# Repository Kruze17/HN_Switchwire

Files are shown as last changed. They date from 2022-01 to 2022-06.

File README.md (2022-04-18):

# HN Switchwire
## Serial Request Video (Playable):
Serial Request (https://www.youtube.com/watch?v=LyNLB14Rkbk)
## This repository hosts the files that are needed to the build my version of the Voron Switchwire from Ender 3 Pro.  

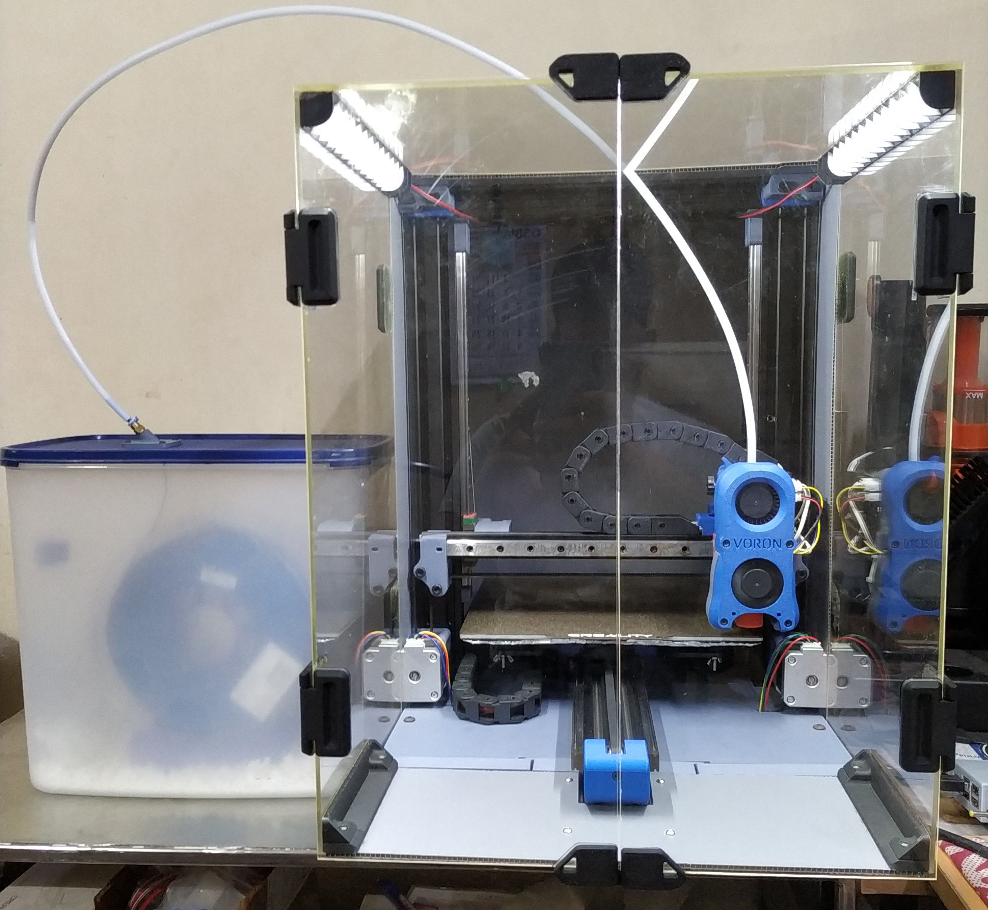
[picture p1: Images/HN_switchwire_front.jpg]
  
### ***These are the repositories you will need to visit in order to get required STL files and more information. I just simply cannot host them in my repo as the creators have put so much effort and time in building and documenting their own versions of designs. Peace.***  
  
[DaRk_dOg's](https://github.com/boubounokefalos) Ender_SW: https://github.com/boubounokefalos/Ender_SW  
[Badnoob's](https://github.com/VoronDesign/VoronUsers/tree/master/printer_mods/Badnoob) AB BN 30: https://github.com/VoronDesign/VoronUsers/tree/master/printer_mods/Badnoob/AB-BN  
~~[M. Kanawati's](https://github.com/kanawati975) BL Touch X-carriage mod for Switchwire: https://github.com/kanawati975/Voron_Switchwire/tree/main/BL-Touch~~  
[henrikssn's](https://github.com/henrikssn) Euler Extruder: https://github.com/henrikssn/VoronUsers/tree/euler/printer_mods/henrikssn/euler_extruder  
[Tripnutz's](https://www.thingiverse.com/tripnutz/designs) ePIc snapPI hinged pi case: https://www.thingiverse.com/thing:2747502
###### Update 09-02-2022
```
1. The X-carriage BL Touch mod for Switchwire was made for e3d V6 Hotend only. So i have decided to drop it.
   After several suggestions regarding the BL touch not perforimg well in a fully enclosed printer, i decided to
   go with an inductive probe. But it's creator M. Kanawati was kind enough to offer me custom design files
   sepcific for my hotend. But as i have said, i am moving towards inductive probe.

2. Added the rail guides for MGN12H linear rails and 4040 extrusion rail guide as per subscribers' request.

3. Added the modified the x-axis drag chain anchor for euler extruder for switchwire, in case you guys want it.
```
###### Update 28-02-2022
```
1. Added my printer's hartk Toolhead PCB rev3.2 wiring diagram with Creality v4.2.2 board.

2. Added my printer's klipper config files for user reference.
```
###### Update 7-03-2022
```
1. Added my printer's slicer configs.
```
###### Update 29-03-2022
```
1. Added the stl file for modified 6mm filament feed slot
2. Added the stl files for my custom pi case
```

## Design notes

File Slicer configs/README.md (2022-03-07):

## Changes that you might want to do to my slicer configs:
### Set your bed dimensions:
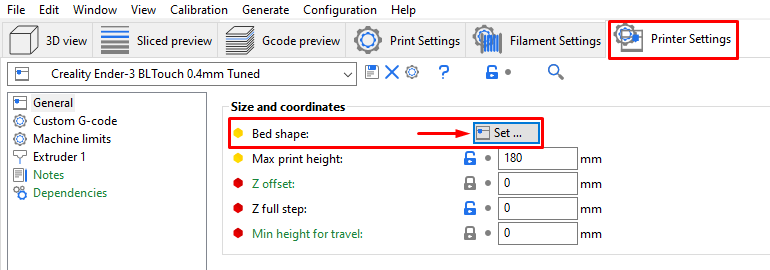
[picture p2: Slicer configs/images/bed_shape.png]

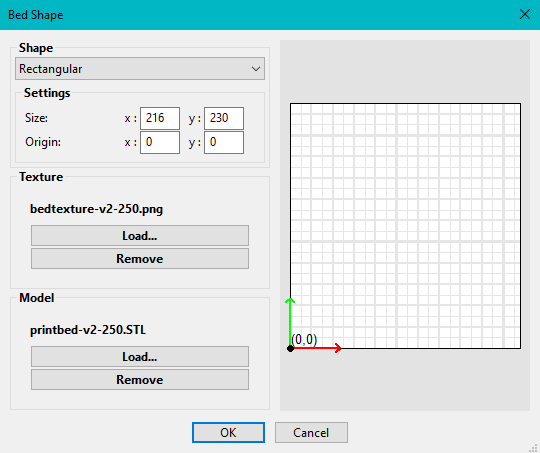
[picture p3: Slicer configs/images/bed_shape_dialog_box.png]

### Load a custom bed texture and model:
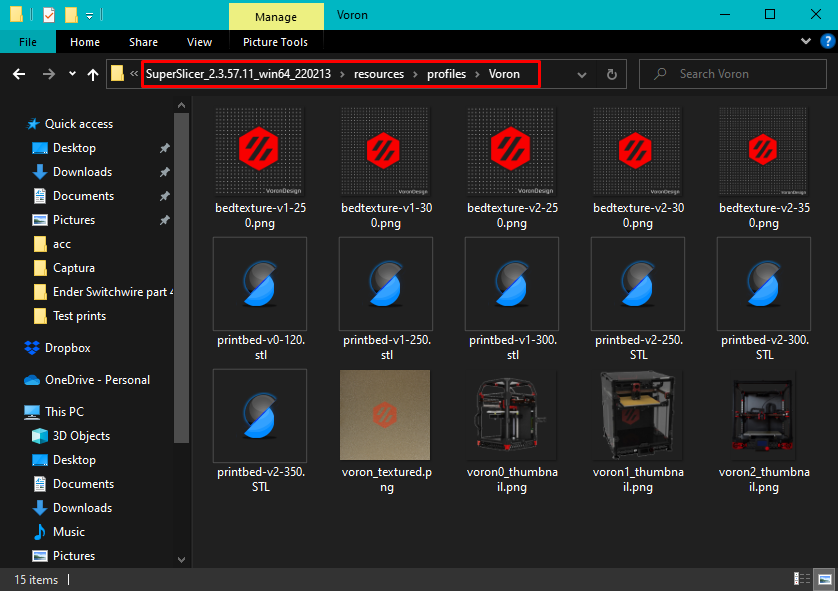
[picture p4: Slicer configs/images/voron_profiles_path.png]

### Change the custom gcode settings:
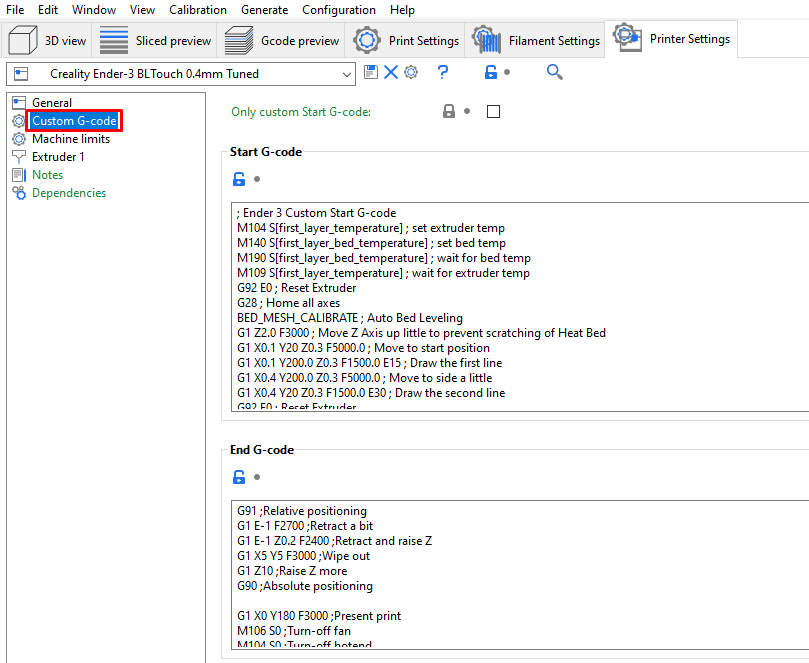
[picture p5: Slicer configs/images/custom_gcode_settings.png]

### Change retraction settings:
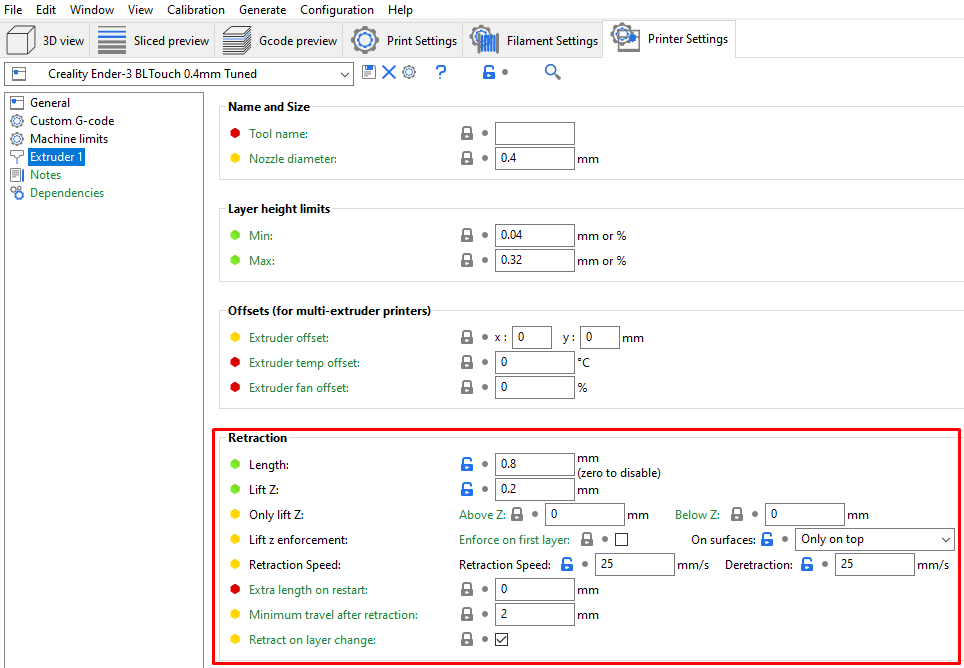
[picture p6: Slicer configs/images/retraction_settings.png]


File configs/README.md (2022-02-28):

## !!! Warning !!!
***Do no copy-paste or blindly use the configs! Use them with proper research and knowledge. I "do not" take any responsibility, if your printer gets damaged by using my configs.***   

I am using GCode shell command extension by [Arksine](https://github.com/Arksine) for my custom macros in client_macros.cfg file: https://github.com/th33xitus/kiauh/blob/master/docs/gcode_shell_command.md

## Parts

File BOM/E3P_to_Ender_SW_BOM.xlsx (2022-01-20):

Category | Component | Standard | Qty | Required for the Ender SW?
Filament | Primary Color (Black) |  | 1 | Yes
Filament | Secondary Color (Red) |  | 1 | Yes
Printed Parts | Printed Parts |  | 1 | Yes - STLs on GitHub (https://github.com/boubounokefalos/Ender_SW)
Fasteners | M2x10 Self Tapping Screw for Plastics |  | 6 | Updated according to Ender_SW BOM
Fasteners | M3x12 SHCS |  | 13
Fasteners | M3x14 BHCS |  | 2
Fasteners | M3x16 SHCS |  | 6
Fasteners | M3x20 SHCS |  | 8
Fasteners | M3x25 SHCS |  | 4
Fasteners | M3x30 SHCS |  | 26
Fasteners | M3x40 SHCS |  | 7
Fasteners | M3x6 FHCS |  | 12
Fasteners | M3x8 SHCS |  | 71
Fasteners | M4x20 SHCS |  | 2
Fasteners | M4x6 BHCS |  | 2
Fasteners | M5x10 BHCS |  | 10
Fasteners | M5x10 SHCS |  | 4
Fasteners | M5x16 BHCS |  | 5
Fasteners | M5x20 BHCS |  | 1
Fasteners | M5x20 SHCS |  | 8
Fasteners | M5x35 BHCS |  | 4
Fasteners | M5x40 SHCS |  | 8
Fasteners | M5x60 SHCS |  | 8
Fasteners | 6x6x3 Aluminium Spacer from Ender 3 |  | 4
Fasteners | M3 Heatset Insert |  | 54
Fasteners | M5 1mm Shim |  | 20
Fasteners | M3 Hexnut |  | 10
Fasteners | M3 T-nut (For 2020 extrusions) |  | 35 | Updated according to Ender_SW BOM
Fasteners | M5 T-nut (For 2020 extrusions) |  | 50 | Updated according to Ender_SW BOM
Motion | GT2 Open Belt LL-2GT-6 (6mm wide) - 1500mm |  | 2 | Yes
Motion | GT2 Open Belt LL-2GT-6 (6mm wide) - 800mm |  | 1 | Yes
Motion | GT2 20T (6mm wide) Pulley (5mm bore) |  | 3 | Yes
Motion | F695 2RS Bearing |  | 20 | Yes
Motion | Linear Rail MGN12H (300mm) |  | 5 | X -> 1, Y -> 2 and Z -> 2
Motion | Key-bak Super48 13oz |  | 1 | Yes
Vibration Management | Rubber Compressor Foot |  | 4 | Yes or you can use these printed feet (https://www.thingiverse.com/thing:4721832)
Electronics | Omron Mouse Button - Micro Switch |  | 2 | 1 - the Y axis microswitch is reused
Electronics | Omron TL-Q5MC2 - NPN, NC, 5mm Sense |  | 1 | Yes
Electronics | BAT85 Diode |  | 1 | Yes
Electronics | NEMA17 Motor 17HS15-1504S1 |  | 3 | New or Reused. If you have a gear puller, you can reuse these. I bought new ones. You also need the smaller motor for the afterburner.
Electronics | Mean Well LRS-350-24 PSU |  | 1 | Reused
Electronics | Mean Well RS-25-5 PSU |  | 1 | Yes
Electronics | ZF - Rocker Switches DPST 16A ON-OFF |  | 1 | No
Electronics | Fuse Medium Time Delay Acting 8A 250V Holder Cartridge 5 X 20mm Glass |  | 2 | Yes
Electronics | TycoElectronics - 10EGG1-2 (Normal) or 10EHG1-2 (Medical): Filtered Power Inlet |  | 1 | No
Electronics | IEC320 C14 Inlet - Push-fit - w/ Rocker Switch & Fuse |  | 1 | Yes
Electronics | 40x40x10 Axial Fan- Ball Bearing (24V) |  | 1 | Yes
Electronics | 40x40x20 Centrifugal Blower Fan - Ball Bearing (24V) |  | 1 | Depends on version of Afterburner
Electronics | 60x60x20 Axial Fan (24V) |  | 1 | Yes
Controller | RaspberryPi4 |  | 1 | Reused ( I was running Octoprint)
Controller | MicroSD Card |  | 1 | Reused
Controller | USB C Power Cable |  | 1 | Reused
Controller | SKR Mini E3 V2 |  | 1 | Reused or new. I had upgraded before the mod
Controller | USB Cable A-male Mini B-male (Included with SKR Mini) |  | 1 | A right angle USB mini is required
Controller | Mini 12864 Display (Type B) |  | 1 | Optional. I don't use one
Frame | Misumi 3060 x 520mm - HFSB6-3060-520-AH105-BH415-AV180 |  | 2 | Use Ender 3 Pro frame
Frame | Misumi 3030 x 400mm - HFSB6-3030-400-TPW |  | 2 | Use Ender 3 Pro frame
Frame | Misumi 3030 x 360mm - HFSB6-3030-360-LCH-RCH |  | 1 | Use Ender 3 Pro frame
Frame | Misumi 3030 x 300mm - HFSB6-3030-300-TPW |  | 2 | Use Ender 3 Pro frame
Frame | Misumi 2020 x 340mm - HFSB5-2020-340-AH15-BH325 |  | 1 | Use Ender 3 Pro frame
Frame | Misumi 2020 x 340mm - HFSB5-2020-340 |  | 1 | Use Ender 3 Pro frame
Misc | Bowden Tube (4mm OD, 3mm ID) |  | 3m | Reused
Misc | 6mm x 3mm Round Neodymium Magnets |  | 8 | No
Cables | Fork Spade Terminal |  | 15 | I have a various assorment of connectors as Voron recommends. The quantities may be off and everyone has their own preferences for wiring Yes
Cables | Insulated Crimp Receptical |  | 10 | Yes
Cables | Nylon Cable Ties 4" |  | 100 | Yes
Cables | MicroFit3 Male Pin (43031-0007) |  | 40 | Yes
Cables | MicroFit3 Female Pin (43030-0007) |  | 40 | Yes
Cables | MicroFit Connector Receptacle 4 Position (43645-0400) |  | 4 | Yes
Cables | MicroFit Connector Receptacle 3 Position (43645-0300) |  | 1 | Yes
Cables | MicroFit Connector Receptacle 2 Position (43645-0200) |  | 6 | Yes
Cables | MicroFit Connector Plug 4 Position (43640-0401) |  | 4 | Yes
Cables | MicroFit Connector Plug 3 Position (43640-0301) |  | 1 | Yes
Cables | MicroFit Connector Plug 2 Position (43640-0201) |  | 6 | Yes
Cables | JST-XH Female Pin |  | 40 | Yes
Cables | JST-XH Connector Plug 4 Position |  | 4 | Yes
Cables | JST-XH Connector Plug 3 Position |  | 4 | Yes
Cables | JST-XH Connector Plug 2 Position |  | 4 | Yes
Cables | 24AWG Silicone Cable (100ft total) |  | 1 | Yes
Cables | 16AWG Silicone Cable (10ft total) |  | 1 | Yes
Cables | 20AWG Silicone Cable (10ft total) |  | 1 | Yes
Cables | 10x11 Cable Chain - Openable (1m) |  | 2 | Yes
Panels | Opaque Enclosure Panels |  | 6 | No (https://www.michaels.com/corrugated-board-by-creatology/M10567770.html)
Panels | Side/Front/Top Acrylic Panels |  | 5 | No (https://www.tapplastics.com/product/plastics/cut_to_size_plastic/acrylic_sheets_clear/508)
Buildplate | Prusa MK52 Heated Bed - 24V |  | 1 | Reused Ender 3 bed
Buildplate | Spring Steel Sheet for Prusa MK52 Bed (included with TL Heated Bed) |  | 1
Buildplate | Prusa MK3 Y Carrier |  | 1
Afterburner |  |  |  | The Afterburner is unchanged. Check the BOM and sourcing guide

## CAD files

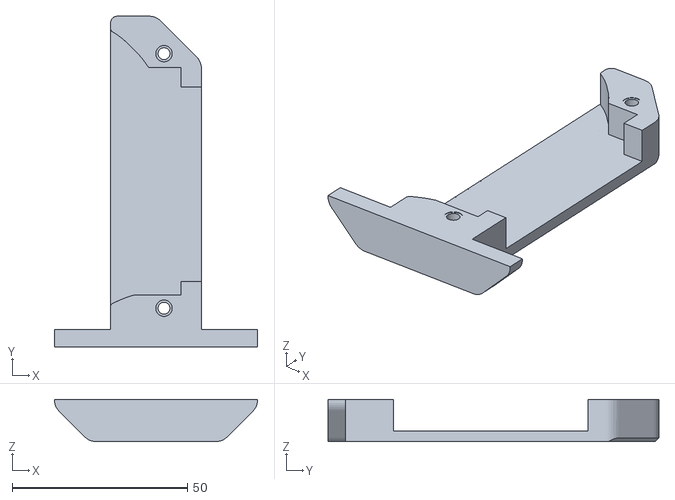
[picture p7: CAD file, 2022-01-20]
Keybak/SW_Alternative_keybak_a.stl
58.0 x 94.5 x 12.0

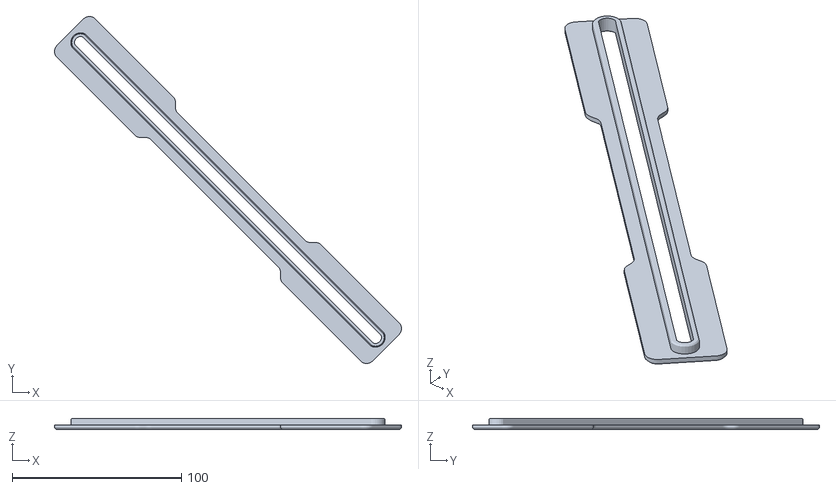
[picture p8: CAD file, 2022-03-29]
Modified feed slot/6mm_feed_slot.stl
205.3 x 205.3 x 6.40

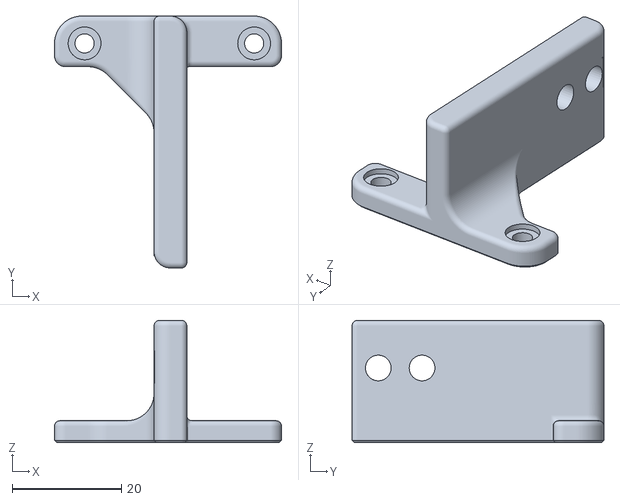
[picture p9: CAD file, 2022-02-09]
Modified X-chain Anchor(igus)/x_chain_anchor_igus_remixed.stl
41.5 x 46.1 x 22.3

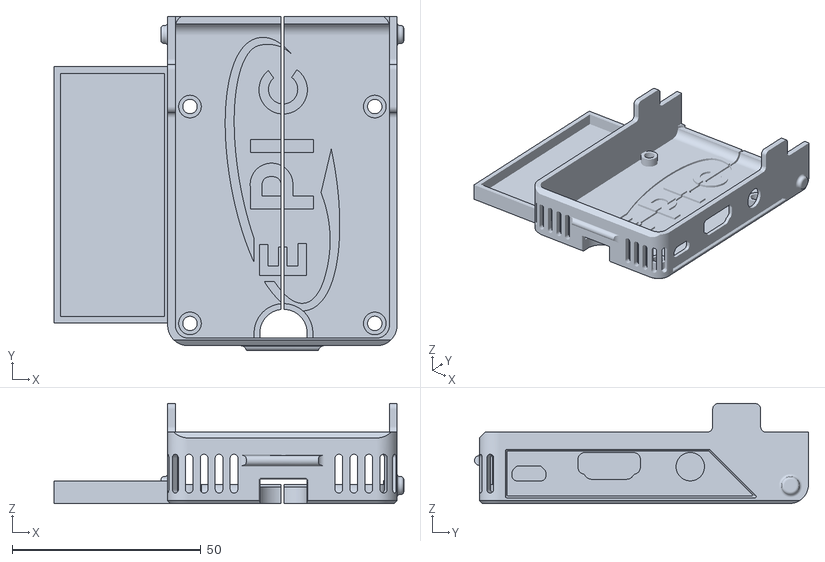
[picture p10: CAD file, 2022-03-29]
Pi 3b+ case/rpi3b+_base_v1.stl
92.7 x 88.6 x 26.5

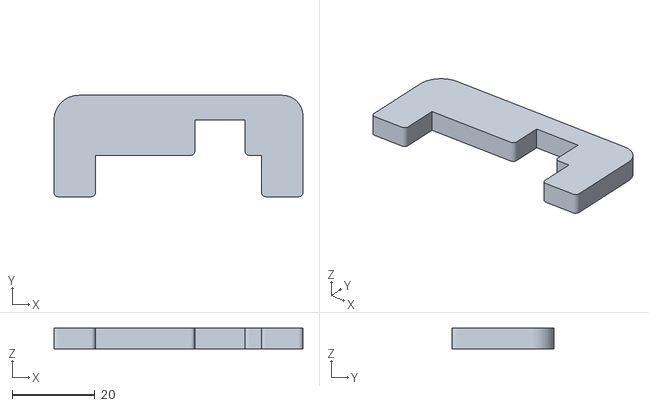
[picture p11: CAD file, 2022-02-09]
Rail Guides/4040_rail_guide_x2.stl
60.1 x 24.5 x 5.00

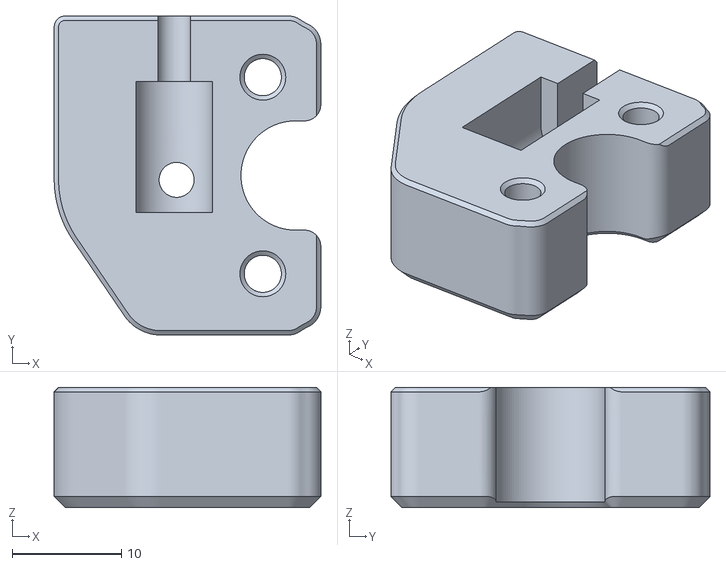
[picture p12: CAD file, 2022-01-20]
Keybak/counterweight_gantry_anchor.stl
24.4 x 29.2 x 11.0

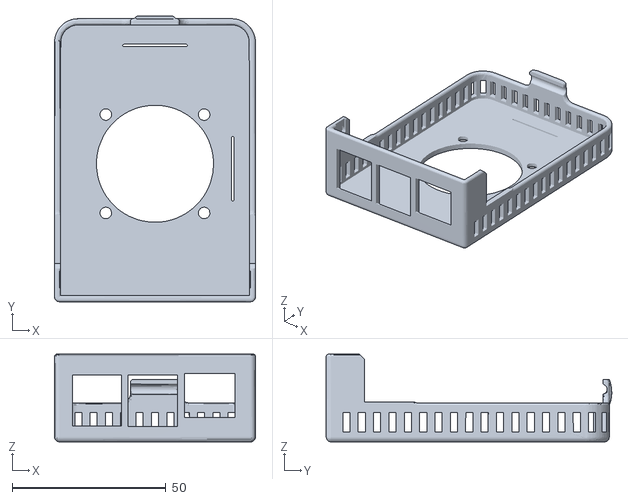
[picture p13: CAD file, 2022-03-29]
Pi 3b+ case/top-cover_4010_v1.stl
65.4 x 92.9 x 28.6

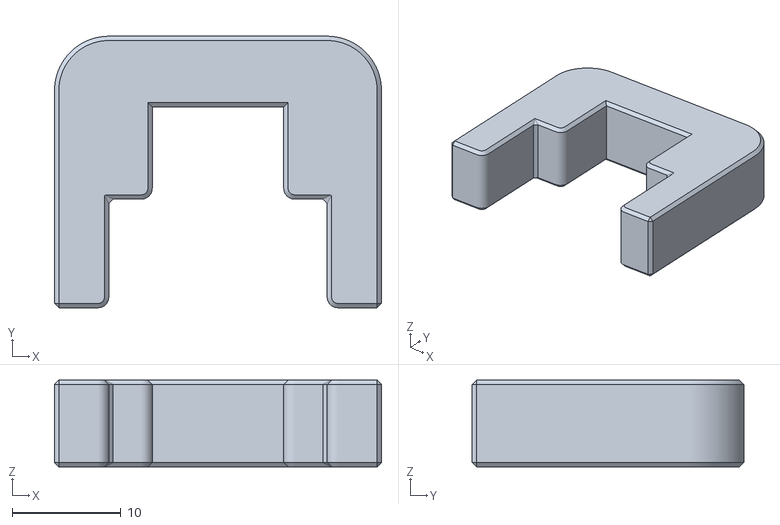
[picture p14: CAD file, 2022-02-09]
Rail Guides/2020_MGN12_rail_guide_x2.stl
30.1 x 25.0 x 8.00

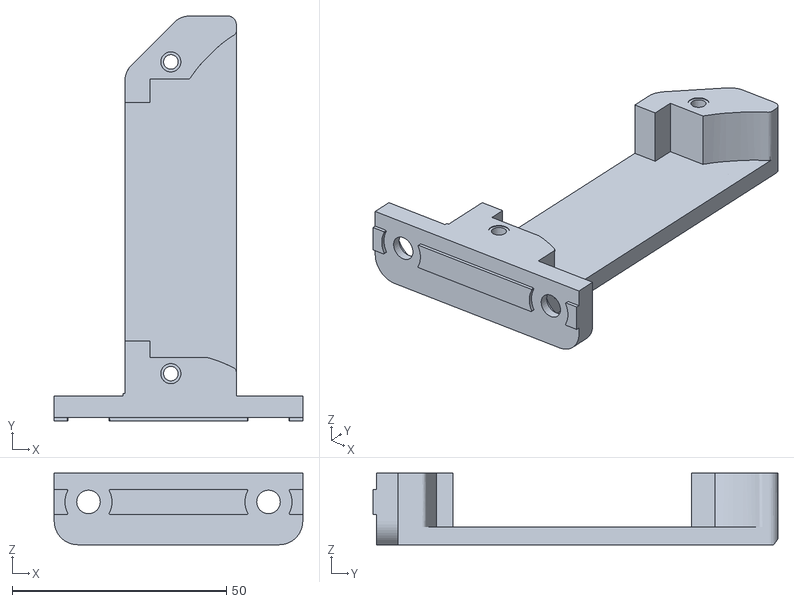
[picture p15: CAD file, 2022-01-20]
Keybak/SW_Alternative_keybak_b.stl
58.0 x 94.5 x 16.7

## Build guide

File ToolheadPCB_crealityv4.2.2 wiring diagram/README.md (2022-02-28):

## Notes on printer mainboard wiring:
```
1. Endstops, sensors and thermistors get connected to the +ve pin of the respective port on printer mainboard.
2. Part cooling fan or any MOSFET driven load gets connected to the -ve pin of the respective port on printer mainboard.
```
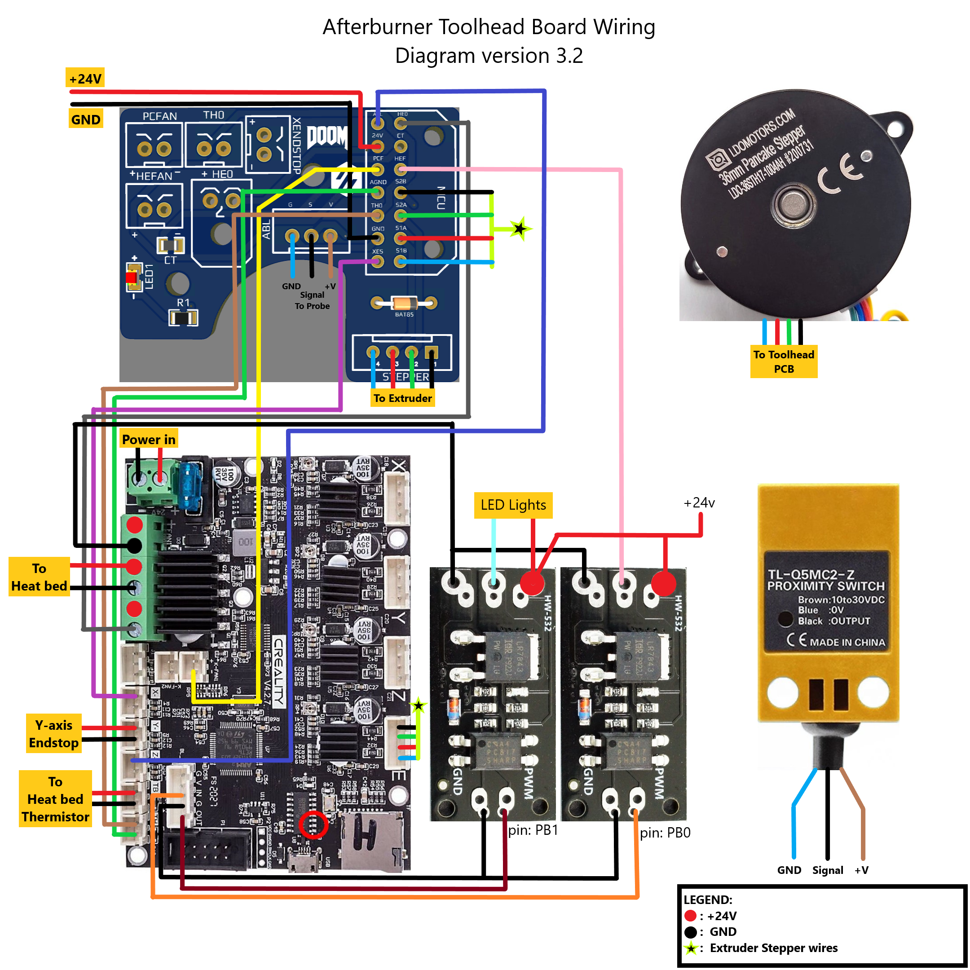
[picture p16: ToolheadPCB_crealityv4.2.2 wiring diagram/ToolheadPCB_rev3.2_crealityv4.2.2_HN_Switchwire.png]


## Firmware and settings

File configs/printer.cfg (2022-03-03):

# This file contains pin mappings for the stock 2020 Creality Ender 3
# Pro with the 32-bit Creality 4.2.2 board. To use this config, during
# "make menuconfig" select the STM32F103 with a "28KiB bootloader" and
# serial (on USART1 PA10/PA9) communication.

# If you prefer a direct serial connection, in "make menuconfig"
# select "Enable extra low-level configuration options" and select
# serial (on USART3 PB11/PB10), which is broken out on the 10 pin IDC
# cable used for the LCD module as follows:
# 3: Tx, 4: Rx, 9: GND, 10: VCC

# Flash this firmware by copying "out/klipper.bin" to a SD card and
# turning on the printer with the card inserted. The firmware
# filename must end in ".bin" and must not match the last filename
# that was flashed.

# See docs/Config_Reference.md for a description of parameters.

#[force_move]
#enable_force_move: True

[homing_override]
axes: z
set_position_z: 0
gcode:
    G90
    G0 Z5 F500
    G28 X0 Y0
    G0 X108 Y115 F9000
    G28 Z0
    G0 Z5 F500
	
[stepper_x]
step_pin: PC2
dir_pin: PB9
enable_pin: !PC3
microsteps: 16
rotation_distance: 40
endstop_pin: ^PA5
position_endstop: 216
position_min: 0
position_max: 216
homing_speed: 50
homing_positive_dir: true

[stepper_y]
step_pin: PB8
dir_pin: !PB7
enable_pin: !PC3
microsteps: 16
rotation_distance: 40
endstop_pin: ^PA6
position_endstop: 0
position_min: 0
position_max: 230
homing_speed: 50
homing_positive_dir: false

[stepper_z]
step_pin: PB6
dir_pin: PB5
enable_pin: !PC3
microsteps: 16
rotation_distance: 40
#endstop_pin: ^PA7
endstop_pin: probe:z_virtual_endstop
#position_endstop: 0.0
position_min: -6
position_max: 175
homing_speed: 10

[extruder]
max_extrude_only_distance: 300.0
step_pin: PB4
dir_pin: PB3
enable_pin: !PC3
microsteps: 16
rotation_distance: 4.500
nozzle_diameter: 0.400
filament_diameter: 1.750
heater_pin: PA1
sensor_type: EPCOS 100K B57560G104F
sensor_pin: PC5
control: pid
# tuned for stock hardware with 200 degree Celsius target
pid_Kp: 21.527
pid_Ki: 1.063
pid_Kd: 108.982
min_temp: 0
max_temp: 265
#min_extrude_temp: 0

[heater_bed]
heater_pin: PA2
sensor_type: EPCOS 100K B57560G104F
sensor_pin: PC4
control: pid
# tuned for stock hardware with 50 degree Celsius target
pid_Kp: 54.027
pid_Ki: 0.770
pid_Kd: 948.182
min_temp: 0
max_temp: 130

[fan]
pin: PA0

[heater_fan nozzle_fan]
pin: PB0
heater: extruder
heater_temp: 50.0
shutdown_speed: 0
fan_speed: 1.0

[temperature_sensor Mainboard]
sensor_type: temperature_mcu
min_temp: 0
max_temp: 100

#[temperature_sensor raspberry_pi]
#sensor_type: temperature_host
#min_temp: 10
#max_temp: 100

[output_pin LIGHTS]
pin: PB1
value: 0
shutdown_value: 0

[probe]
pin: PA7
x_offset: 0.0
y_offset: 24.0
z_offset: 0.0
samples: 3
samples_result: median
speed: 8

[mcu]
serial: /dev/ttyPrinter
restart_method: command

[printer]
kinematics: corexz
max_velocity: 300
max_accel: 4000
max_accel_to_decel: 2000
max_z_velocity: 50
max_z_accel: 1000
square_corner_velocity: 4.0

[bed_mesh]
speed: 150
horizontal_move_z: 4
mesh_min: 10,24
mesh_max: 216,222
probe_count: 5,5
algorithm: bicubic
fade_start: 1
fade_end: 10
fade_target: 0

#Manual Bed-Screw Leveling
[bed_screws]
screw1: 23,3
screw1_name: Front Left
screw2: 23,175
screw2_name: Rear Left
screw3: 195,175
screw3_name: Rear Right
screw4: 195,3
screw4_name: Front Right
screw5: 108,115
screw5_name: Center
speed: 150

#Bed screws adjust using the probe
[screws_tilt_adjust]
screw1: 23,3
screw1_name: front left screw
screw2: 23,175
screw2_name: rear left screw
screw3: 195,175
screw3_name: rear right screw
screw4: 195,3
screw4_name: front right screw
speed: 120
screw_thread: CW-M4

#[safe_z_home]
#home_xy_position: 117.5,117.5 # Change coordinates to the center of your print bed
#home_xy_position: 158.5,127.5  # Change coordinates to the center of your print bed
#z_hop: 10                      # Move up 10mm 
#z_hop_speed: 5

[display]
lcd_type: st7920
cs_pin: PB12
sclk_pin: PB13
sid_pin: PB15
encoder_pins: ^PB14, ^PB10
click_pin: ^!PB2

[include client.cfg]
[include client_macros.cfg]

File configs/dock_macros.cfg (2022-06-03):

###############################################################################
####                          Edit this section                            ####
###############################################################################

[gcode_macro GlobalVariables]

# Location of the probe when docked.  
variable_dock_x: 216        # X location
variable_dock_z: 24         # Z location

# What other way can you home the Z-Axis (prior to attaching the probe)? Use 3 ONLY if
# you can have the X-carriage and toolhead clear of the bed when the gantry is resting
# on the lower Z end blocks with the bed pushed all the way to the rear
variable_initial_homing: 1  # 1(none/probe only), 2(Z-max microswitch endstop), 3(Z-min microswitch endstop)

variable_dock_x_offset: 27  # The distance to move along x when docking/undocking the probe from the dock
variable_dock_z_offset: 10  # The distance to move along z when attaching/detaching the probe to/from the toolhead

# Travel and Dock speeds
variable_travel_speed: 9000 # Travel speed
variable_dock_speed: 6000   # Docking maneuvers speed

gcode:

###############################################################################
####                     Do not change the lines below                     ####
###############################################################################

[homing_override]
axes: xyz
gcode:
    #LIGHTS_ON
    SET_GCODE_OFFSET Z=0
    query_probe
    do_Home

[gcode_macro do_Home]
gcode:
    GlobalVariables
    {% set dock_x = printer["gcode_macro GlobalVariables"].dock_x %}
    {% set dock_z = printer["gcode_macro GlobalVariables"].dock_z %}
    {% set dock_z_offset = printer["gcode_macro GlobalVariables"].dock_z_offset %}
    {% set travel_speed = printer["gcode_macro GlobalVariables"].travel_speed %}
    {% set initial_homing = printer["gcode_macro GlobalVariables"].initial_homing %}

    {% if printer.toolhead.homed_axes == 'xyz' %}
        G90
        G0 Z{ dock_z + dock_z_offset } F{ travel_speed }                
        
        G28 X0 Y0
        
        Attach_probe
        PROBE_HOMING

	{% else %}
        SET_KINEMATIC_POSITION X={ dock_x } Z=0
        G90
        G0 Z{ dock_z + dock_z_offset } F{ travel_speed }
                
        G28 X0 Y0

        {% if printer.probe.last_query == 0 %}
            PROBE_HOMING
        {% endif %}

        {% if printer.probe.last_query == 1 %}
            {% if initial_homing == 1 %}
                RESPOND TYPE=error MSG="Please attach probe"
                M117 Please attach probe
            {% endif %}
            {% if initial_homing == 2 %}
                SENSORLESS_HOMING
            {% endif %}
            {% if initial_homing == 3 %}
                PROBELESS_HOMING
            {% endif %}
	        {% if initial_homing == 4 %}
                PROBELESS_HOMING
            {% endif %}
        {% endif %}
    {% endif %}

[gcode_macro PROBELESS_HOMING]
gcode:
    GlobalVariables
    {% set dock_z = printer["gcode_macro GlobalVariables"].dock_z %}
    {% set dock_z_offset = printer["gcode_macro GlobalVariables"].dock_z_offset %}
    {% set travel_speed = printer["gcode_macro GlobalVariables"].travel_speed %}
    {% set home_x = printer.configfile.config.stepper_x.position_max|int %}
    {% set home_y = printer.configfile.config.stepper_y.position_max|int %}
    {% set probe_y_offset = printer.configfile.settings.probe.y_offset %}
    {% set y_min = printer.configfile.settings.stepper_y.position_min %}
    {% set initial_homing = printer["gcode_macro GlobalVariables"].initial_homing %}

    {% if initial_homing == 3 %}
        G0 X{ home_x / 2 } Y{ y_min + 5 } F{ travel_speed }
    {% endif %}

    {% if initial_homing == 4 %}
        G0 X{ home_x / 2 } Y{ home_y / 2 - probe_y_offset } F{ travel_speed }
    {% endif %}

    G28 Z0
    G0 Z{dock_z + dock_z_offset } F{ travel_speed }
    Attach_probe
    Adjust_Z

[gcode_macro PROBE_HOMING]
gcode:
    Adjust_Z

[gcode_macro Adjust_Z]
gcode:
    GlobalVariables
    {% set travel_speed = printer["gcode_macro GlobalVariables"].travel_speed %}
    {% set home_x = printer.configfile.config.stepper_x.position_max|int %}
    {% set home_y = printer.configfile.config.stepper_y.position_max|int %}
    {% set probe_y_offset = printer.configfile.settings.probe.y_offset %}
    {% set z_max = printer.configfile.config.stepper_z.position_max %}
    {% set probe_offset_z = printer.configfile.config.probe.z_offset|float %}

    G0 X{ home_x / 2 } Y{ home_y / 2 - probe_y_offset } F { travel_speed }
    SET_KINEMATIC_POSITION Z={ z_max }
    PROBE PROBE_SPEED=10
    SET_KINEMATIC_POSITION Z={ probe_offset_z }
    G91
    G0 Z2 F{ travel_speed }
    G90
    PROBE PROBE_SPEED=5
    SET_KINEMATIC_POSITION Z={ probe_offset_z }
    G0 Z{ probe_offset_z + 3 } F{ travel_speed }

[gcode_macro Dock_probe]
gcode:
    query_probe
    do_Dock

[gcode_macro do_Dock]
gcode:
    {% if printer.probe.last_query == 1 %}
        RESPOND PREFIX= MSG="Probe is already docked!"
        M117 Probe is already docked!

    {% else %}
	    GlobalVariables
        {% set dock_x = printer["gcode_macro GlobalVariables"].dock_x %}
        {% set dock_z = printer["gcode_macro GlobalVariables"].dock_z %}
        {% set home_y = printer.configfile.config.stepper_y.position_max|int %}
        {% set dock_x_offset = printer["gcode_macro GlobalVariables"].dock_x_offset %}
        {% set dock_z_offset = printer["gcode_macro GlobalVariables"].dock_z_offset %}
        {% set travel_speed = printer["gcode_macro GlobalVariables"].travel_speed %}
        {% set dock_speed = printer["gcode_macro GlobalVariables"].dock_speed %}
        {% set probe_y_offset = printer.configfile.settings.probe.y_offset %}

        {% if printer.toolhead.homed_axes != 'xyz' %}
	        G28	# Home All Axes
	    {% endif %}

        G90
        G0 Z{ dock_z + dock_z_offset } F{ travel_speed }
        G0 X{ dock_x } Y{ home_y / 2 - probe_y_offset } F{ dock_speed }
        G0 Z{ dock_z } F{ dock_speed }
        G0 X{ dock_x - dock_x_offset } Y{ home_y / 2 - probe_y_offset } F{ dock_speed }
        G0 Z{ dock_z } F{ travel_speed }
    {% endif %}

    verify_Docking

[gcode_macro verify_Docking]
gcode:
    query_probe
    safe_Dock

[gcode_macro safe_Dock]
gcode:
    {% if printer.probe.last_query != 1 %}
        M112
    {% endif %}

[gcode_macro Attach_probe]
gcode:
    query_probe
    do_Attach

[gcode_macro do_Attach]
gcode:
    {% if printer.probe.last_query == 0 %}
        RESPOND PREFIX= MSG="Probe is already attached!"
        M117 Probe is already attached!

    {% else %}
        GlobalVariables
        {% set dock_x = printer["gcode_macro GlobalVariables"].dock_x %}
        {% set dock_z = printer["gcode_macro GlobalVariables"].dock_z %}
        {% set dock_x_offset = printer["gcode_macro GlobalVariables"].dock_x_offset %}
        {% set dock_z_offset = printer["gcode_macro GlobalVariables"].dock_z_offset %}
        {% set travel_speed = printer["gcode_macro GlobalVariables"].travel_speed %}
        {% set dock_speed = printer["gcode_macro GlobalVariables"].dock_speed %}
        {% set home_y = printer.configfile.config.stepper_y.position_max|int %}
        {% set probe_y_offset = printer.configfile.settings.probe.y_offset %}

        {% if printer.toolhead.homed_axes != 'xyz' %}
	        G28	# Home All Axes
	    {% endif %}
        
        G90
        G0 X{ dock_x - dock_x_offset } F{ travel_speed }
        G0 Z{ dock_z } F{ travel_speed }
        G0 X{ dock_x } Y{ (home_y / 2) - probe_y_offset } F{ dock_speed }
        G0 Z{ dock_z + dock_z_offset } F{ dock_speed }
        G0 X{ dock_x - dock_x_offset } Y{ home_y / 2 - probe_y_offset } F{ dock_speed }
        G0 Z{ dock_z } F{ travel_speed }
    {% endif %}

[gcode_macro Park_toolhead]
gcode:
    query_probe
    do_Park
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

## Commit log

2022-01-20 Added an un-official BOM
    [E3P_to_Ender_SW_BOM.xlsx]
2022-01-20 Added alternative door closer keybak
    [SW_Alternative_keybak_a.stl, SW_Alternative_keybak_b.stl, counterweight_gantry_anchor.stl]
2022-02-09 Added a remixed x-chain anchor for switchwire
    [x_chain_anchor_igus_remixed.stl]
2022-02-28 Added config files
    Do not copy paste blindly! Use the configs with proper research and knowledge. I do not take any responsibility if your printer gets damaged.
    [client.cfg, client_macros.cfg, printer.cfg]
2022-02-28 Added ToolheadPCB_rev3.2 wiring diagram
2022-03-29 Added a modified 6mm filament feed slot
    [6mm_feed_slot.stl]
2022-03-29 Added the stl files for my custom pi 3b+ case
    [rpi3b+_base_v1.stl, top-cover_4010_v1.stl]
2022-03-29 Added profile images of my printer
2022-06-03 Added the dock_macros for modified Quickdraw
    [dock_macros.cfg]
